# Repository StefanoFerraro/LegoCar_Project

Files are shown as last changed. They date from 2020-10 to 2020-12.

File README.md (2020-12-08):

# **LegoCar Project**

Lego Car Demo (https://www.youtube.com/watch?v=NI2pKg-ZRkI)

**^^^ Click for opening the video**

Inspired by the Donkey Car project, I introduce the Lego Car project. The goal of the project is to design and develop an autonomous car build with elementary pieces of Lego and keeping everything else on a budget.

From the hardware side, the system is based on: **Raspberry Pi4b** for controlling the motors (steering / throttling) and running the perception algorithms  + **L298n** as motor driver + **Picamera** for perception + **Xbox360 Controller** used for manual control/autopilot enable. 

The software development is based on the **ROS** framework, code has been written both in **C++** and **Python**. Driver/Controller libraries has been written for this specific hardware/configuration (feel free to ask if you need help with your specific configuration).

## **1 - Software Overview**

### **1.1 - Structure**

* [**l298n_drive**](l298n_drive): ROS package (C++) for interpreting /cmd_vel messages and converting it into actual motion.
* [**xb360_teleop_interface**](xb360_teleop_interface): ROS package (C++) for interpreting /joy messages and converting it into a /cmd_vel message.
* [**lane_detection**](lane_detection): ROS package (Python) running the perception algorithm. 

### **1.2 - Packages Dependencies**

The following project require the integration of existing ROS packages/libraries:
* [**WiringPi**](http://wiringpi.com/): ROS library (C) for RPi GPIO access
* [**raspicam_node**](https://github.com/UbiquityRobotics/raspicam_node): ROS package for image acquisition from Picamera, the image stream is published as a message of type Sensor_msgs/CompressedImage. 

## **2- Hardware Overview**

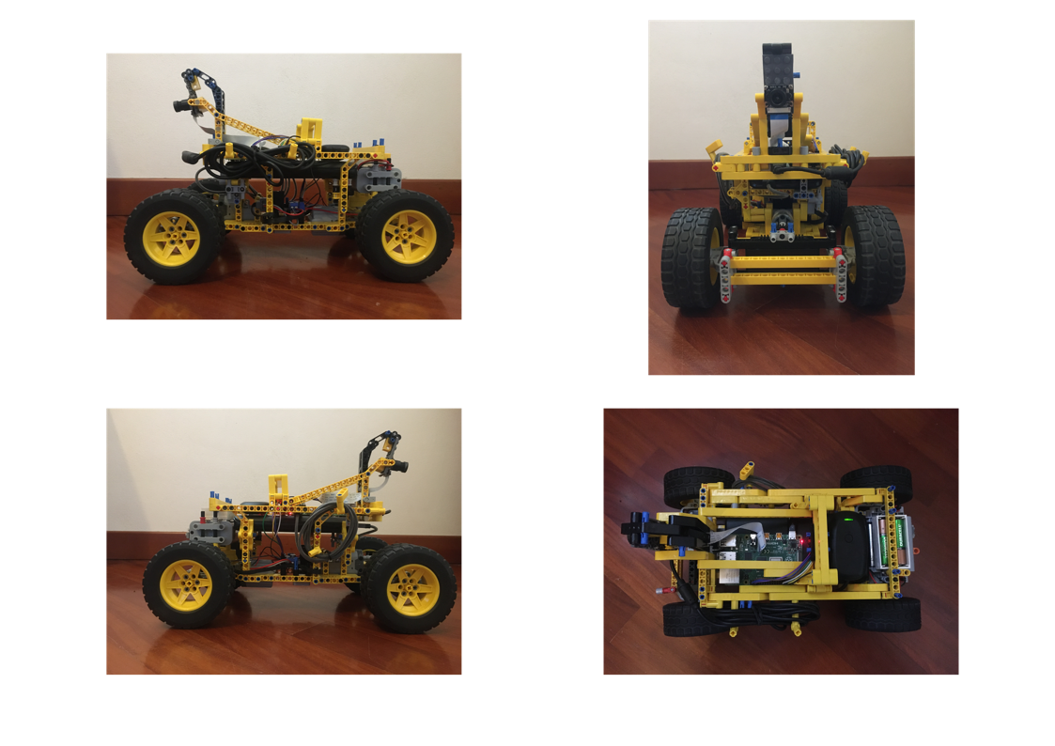
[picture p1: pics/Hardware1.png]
Hardw1


The Lego car model has been custom build for this specific project, it consist of a rear traction system (with differential steering), and a simple steering system in the front. A good starting point for a similar design is proposed here: [Fast and Compact LEGO PF RC car](https://www.youtube.com/watch?v=oS-6K2MqfjM). All the Lego pieces used in the construction were already available to me, almost all the parts comes from the 42030 Lego kit. The overall design of the car presented in this project is the result of multiple iterations. 

### **2.1 - Motors and Battery Pack**
A [Lego Power Function XL Motor](https://www.lego.com/it-it/product/lego-power-functions-xl-motor-8882) has been used for the traction system. For the steering system, a servo motor was needed in order to have precise control over the steering angle, I opted for a [Lego Power Function Servo Motor](https://www.lego.com/it-it/product/power-functions-servo-motor-88004), this specific motor has 15 fixed positions from +90° to -90°. 

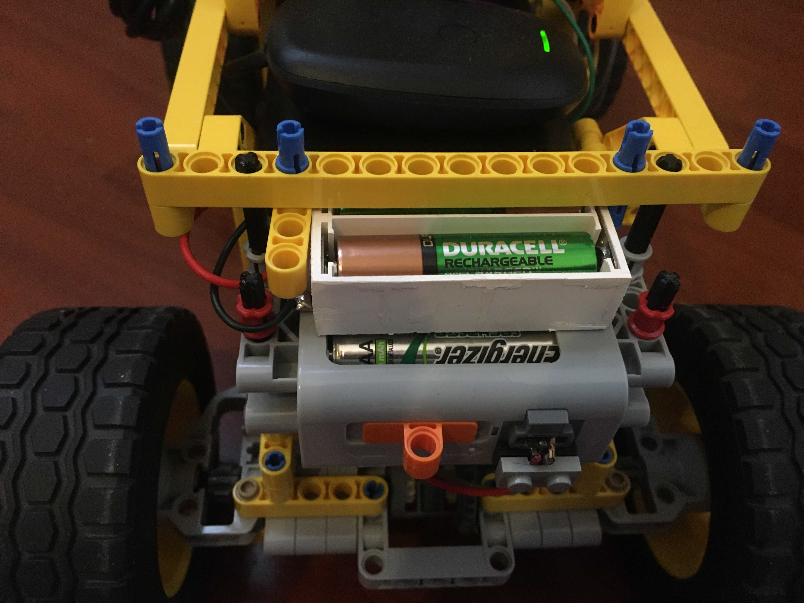
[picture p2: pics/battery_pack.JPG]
battery


Both motors are powered via the [Lego Battery Box](https://www.lego.com/it-it/product/lego-power-functions-battery-box-8881), that has been extended with two batteries in series for a total of 8, this in order to output the required voltage of 9V (Lego recommend 9V for this motors), also with rechargeable Ni-MH batteries (1.2V): 



This mod is not needed in case of non-rechargeable Ni-MH batteries (1.5V): 



In the long run the rechargeable solution is preferable due to the high demand of power (with the rechargeable solution I run the system for approx. 30 minutes before having a consistent decrease in maximum speed).

In order to connect all the components without rewiring all the cables, and therefore limiting the future use of the motor, I come up with a clamping system that consist of forcing the reinforced cable end into the desired pin and taking everything in place thanks to a modifies Lego flat 2x1.  

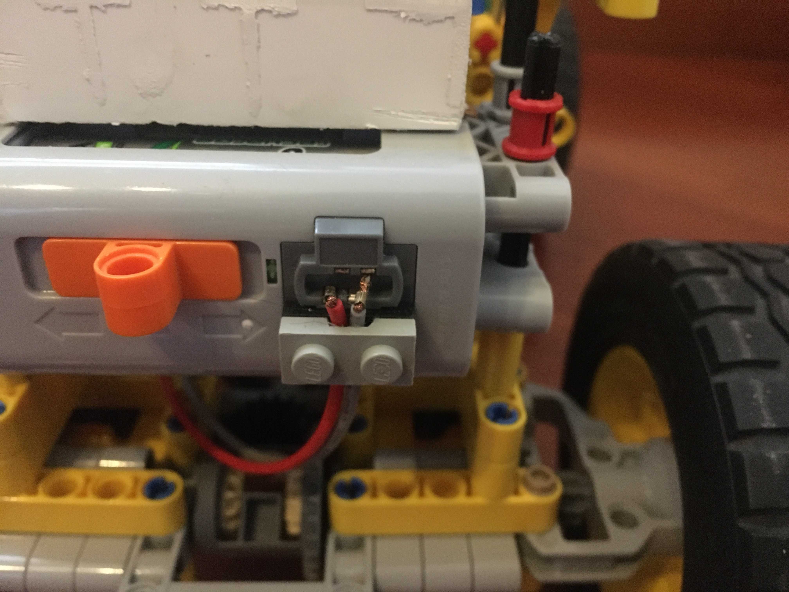
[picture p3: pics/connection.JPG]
connect


### **2.2 - Motors Driver**

A **L298n** module is used in order to control the XL function motor and the Servo one. The later has a control electronics slightly different from the classic 3 wires servo, it consist of 4 wires, one wire controls the servo in the clockwise direction (0..+90°) and the other along the anti-clockwise (0..-90°).

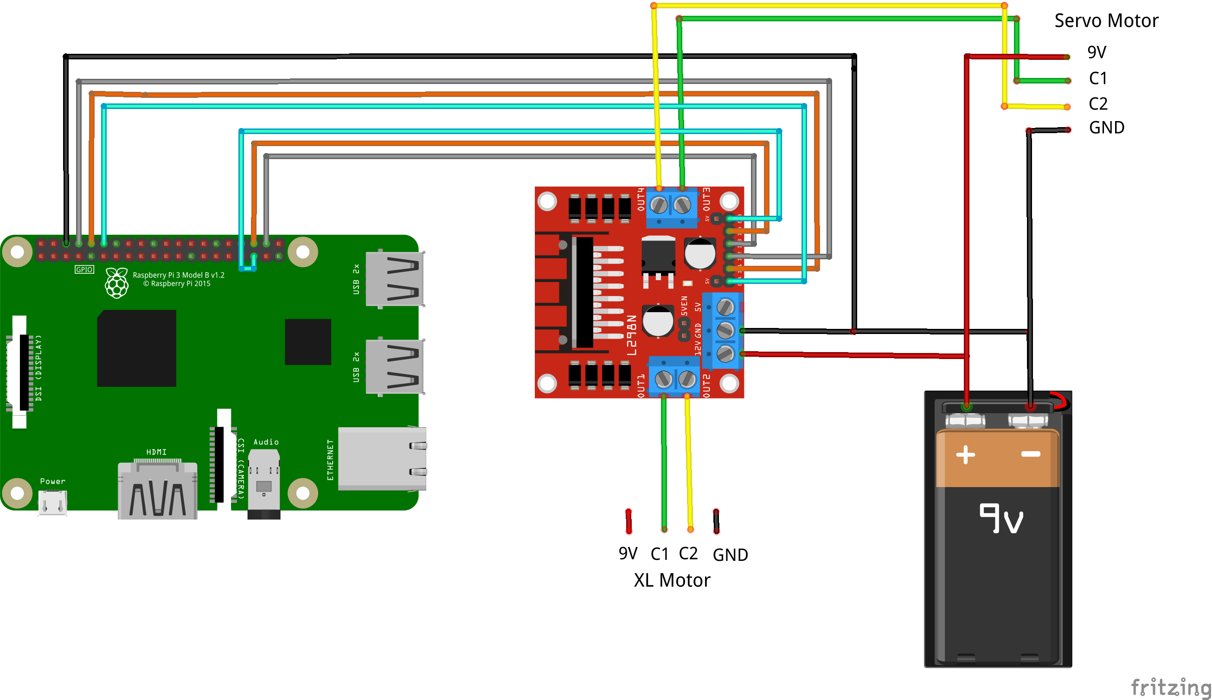
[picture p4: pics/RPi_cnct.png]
wiring


motor_detail

As a reference for the wiring and further technical information about Lego motors/servo: [Lego Technical Information](https://www.philohome.com/tech.htm). Below, the Lego connector scheme is shown:  

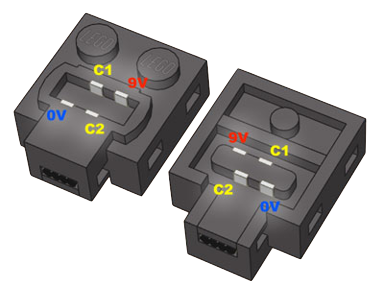
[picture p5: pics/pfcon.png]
lego_wires


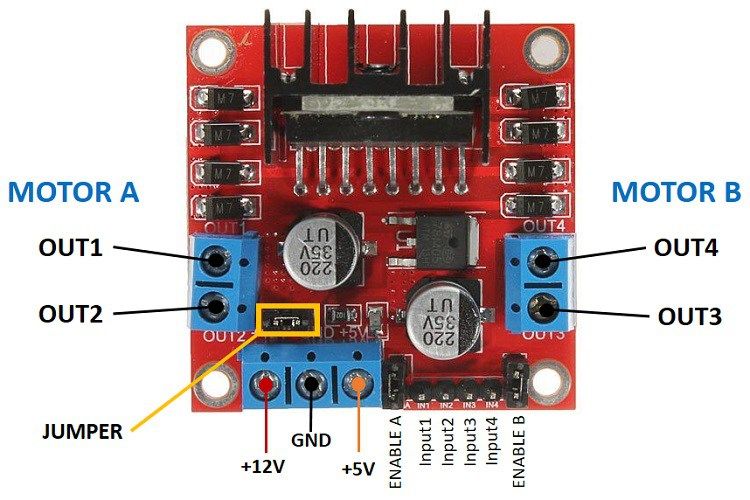
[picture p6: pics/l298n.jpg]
l298n


`OUT3` and `OUT4` of the l298n are wired respectively to `C1` and `C2` of the servo. The same applies to `OUT1` and `OUT2` for control ports of the XL motor. 

In a **DC motor (XL motor)** RPM (Revolutions-Per-Minute) can be module controlling the voltage. PWM (Pulse-Width-Modulation) signal can be used to control the voltage that goes through the motor. Varying the duty cycle of the PWM signal varies also the average voltage outputed (i.e. RPM of motor). 

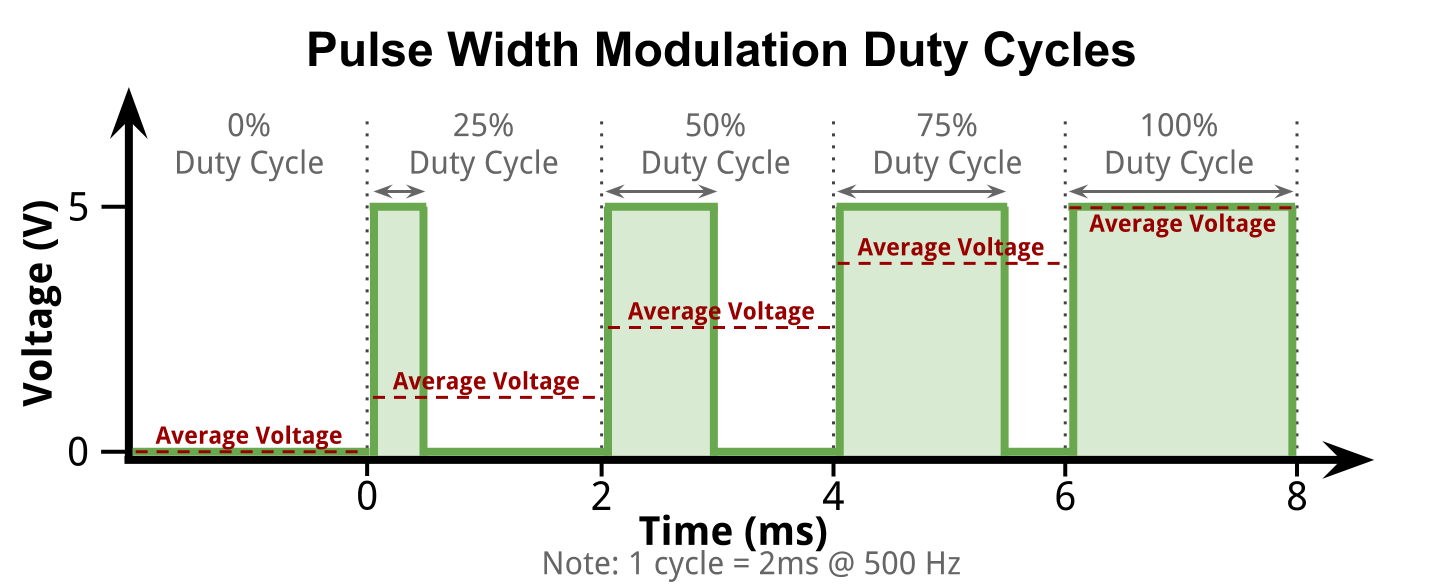
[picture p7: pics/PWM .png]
PWM


With respect of the l298n functional scheme, `Input1` and `Input2` are used for controlling forward/backward direction instead the PWM signal is sent through the `EnableA` pin for the RPM control. Here is a summary table for the control of the XL motor:

| Motion | Input1 | Input2 | EnableA (PWM duty cycle %) |
|---|---|---|---|
| Forward  | 1 | 0 | 0..100 |
| Backward | 0 | 1 | 0..100 |
| Brake | 1 | 1 | 100 |
| Float | 0 | 0 | 0 |

**Servo modules** exploits PWM signals for controlling the position of the axis. In a servo each fixed position of the axis correspond to a specific duty cycle, usually in a common servo system the control goes from -90° to +90° using just one wire. As previously said, in the Lego Servo motor we have 2 control wires, one for clockwise positions and the other for anti-clockwise, here the principle is well presented: [Controlling LEGO Power Functions Servo Motor](https://www.youtube.com/watch?v=XQskgJjk5S4).  

With respect of the l298n functional scheme, `Input3` and `Input4` are used for controlling clockwise/anticlockwise direction instead the PWM signal is sent through the `EnableB` pin for the position control. Here is a summary table for the control of the Servo motor:

| Position | Input3 | Input4 | EnableB (PWM duty cycle %) |
|---|---|---|---|
| 7 (90°) | 0 | 1 | 100 |
| 6 | 0 | 1 | 88.2 |
| 5 | 0 | 1 | 76.0 |
| 4 | 0 | 1 | 63.5 |
| 3 | 0 | 1 | 50.1 |
| 2 | 0 | 1 | 38.0 |
| 1 | 0 | 1 | 25.8 |
| 0 (0°) | 0 | 0 | 0 |
| -1 | 1 | 0 | 25.8 |
| -2 | 1 | 0 | 38.0 |
| -3 | 1 | 0 | 50.1 |
| -4 | 1 | 0 | 63.5 |
| -5 | 1 | 0 | 76.0 |
| -6 | 1 | 0 | 88.2 |
| -7 (-90°)  | 1 | 0 | 100 |

**Raspberry Pi4** has 4 IO that can output hardware PWM signals (as reference see: [Raspberry Pi GPIO](https://www.raspberrypi.org/documentation/usage/gpio/)). In this project I have used (in BCM notation) GPIO19 and GPIO18 as output PWM channels, GPIO14, GPIO15, GPIO16, GPIO20 as standard output channels.  

### **2.3 - PiCamera**

The camera used was already available to me (reused from another project), it has a 75° vision angle, with IR features ([Camera Link](https://it.banggood.com/Camera-Module-For-Raspberry-Pi-4-Model-B-or-3-Model-B-or-2B-or-B+-or-A+-p-1051437.html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)). In the donkey car project they are using a wide angle lens (120/150° angle) in order to get a better vision around the car, this can be useful in order to have more information about the environment in one pic, but also can 'distract' the perception algorithm with useless informations. We will discuss further this aspect in the perception algorithm repo.

The camera, has been fixed using little screws onto a planar lego piece, that is part of a adjustable inclination mount.

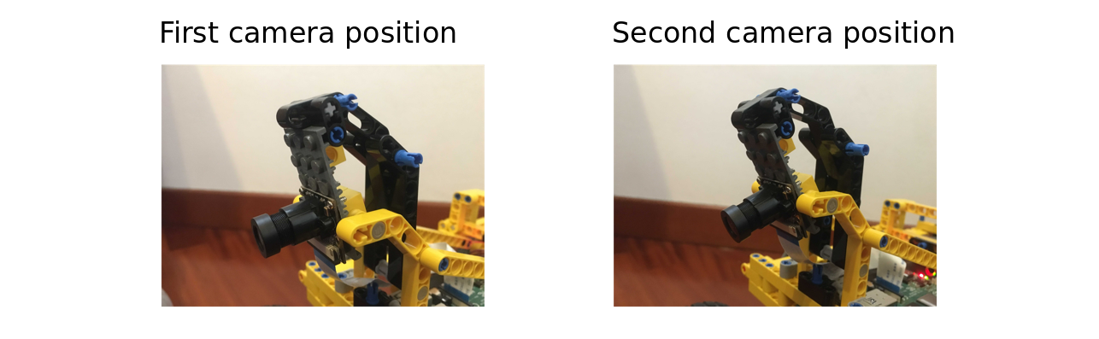
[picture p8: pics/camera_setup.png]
camera_setup


### **2.4 - RPi and Xbox Controller**

The Raspberry Pi is powered by a second battery that outputs 5V/3A as requested by the RPi. The battery serves also as mounting support for the RPi and the controller receiver.

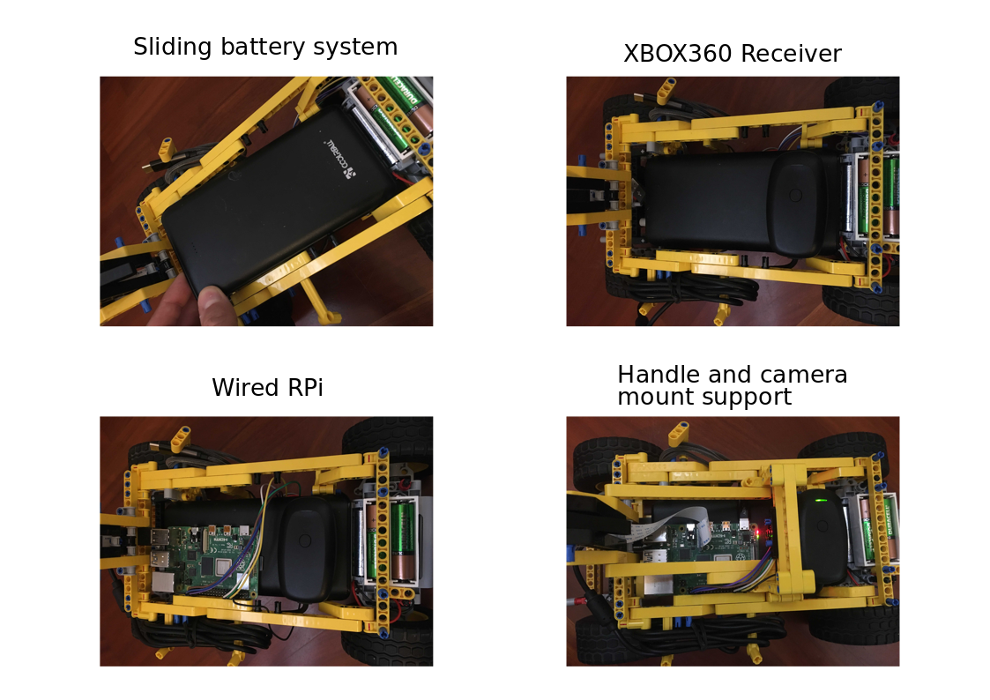
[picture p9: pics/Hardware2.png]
hardware2


In the images above the is shown the sliding system of the battery, this guarantee an easy access to the electronics below when needed. The Xbox360 receiver is fixed in place using patafix. An handle has been designed in order easily transport the car manually.

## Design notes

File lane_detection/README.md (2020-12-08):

# **Lane Detection**

Lego Car Demo (https://www.youtube.com/watch?v=NI2pKg-ZRkI)

**^^^ Click for opening the video**
 
The package provide lane detection functionalities for the compressed image coming from the `raspicam_node`. A direction angle is computed and outputted with the topic `/steering_angle`. A processed image is published to the `/lane_detection/image/compressed` topic.
The Implementation presented is based on several filters applied to the image, and the subsequent application of Canny algorithm + Hought transform. 

## **1 - Main dependencies**
 
* sensor_msgs/CameraInfo
* sensor_msgs/CompressedImage
* rospy
* numpy
* opencv (cv2)
* line_detect/steering_angle

## **2 - Functionalities**

The package subscribe to the topic `/raspicam_node/image/compressed` (type sensor_msgs/CompressedImage), published by the raspicam_node package. Messages are published on topic `/steering_angle`, a custom message designed for passing direction information to the PD controller.

The acquired image go through a specific pipeline in order to extract the the lane/s from the scene. Lanes are then implied in the computation of a direction vector for the LegoCar. The output of the pipeline process is then published to the `/lane_detection/image/compressed` topic.

The pipeline of the image analysis process is:

 1. **Image acquisition and undistortion process**
 2. **Filtering image (blacks)**
 3. **Edge detection wt Canny algorithm**
 4. **ROI + Lines detection wt Hough transform**
 5. **Computation of middle line**
 
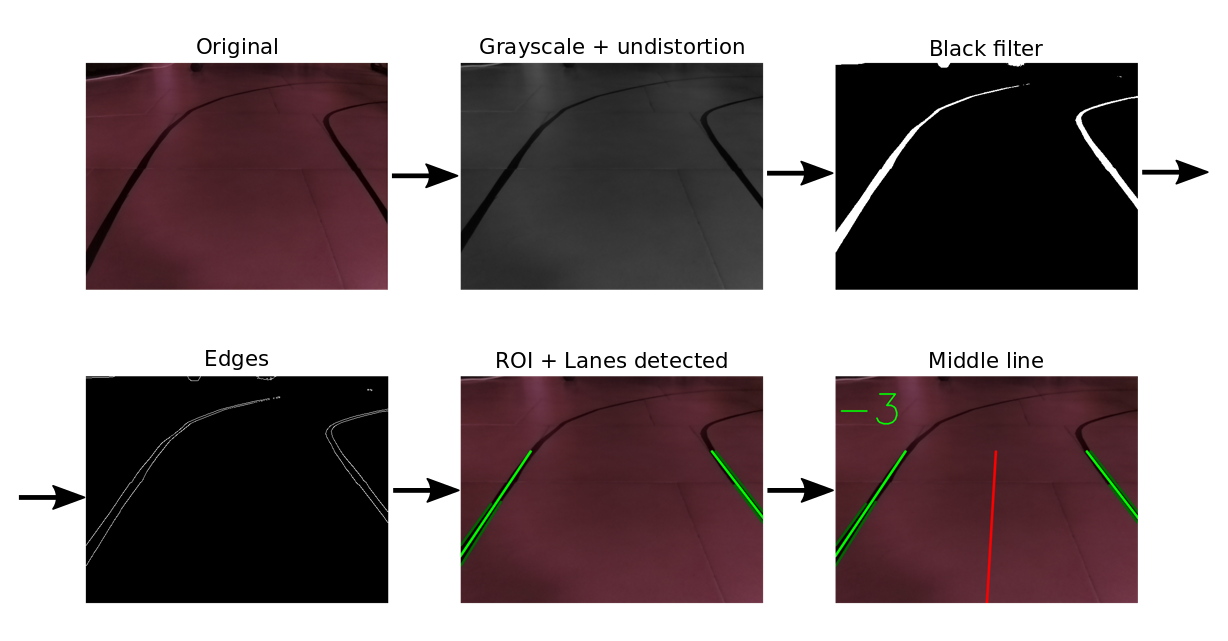
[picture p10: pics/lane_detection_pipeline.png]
 

### **2.1 - Image acquisition and undistortion process** 

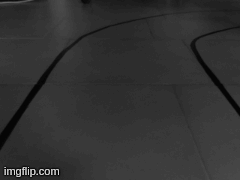
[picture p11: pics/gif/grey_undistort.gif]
greygif
 
 
Cameras transform 3D space information into a 2D form. Since this process is not perfect (due to the imperfect production process of the lenses), we cannot trust the information coming straight from the camera as it is. Our goal is to position the car in space, in order to do it properly the camera matrix and the distortion coefficient needs to be computed and both compensated.
 
The `raspicam_node` package contains a calibration tool, called [`camera_calibration`](https://github.com/UbiquityRobotics/raspicam_node), a calibration maze is needed for this process. Once the process is completed a `.yaml` file is generated. Follows an example:

````
image_width: 640
image_height: 480
camera_name: camerav2_640x480
camera_matrix:
  rows: 3
  cols: 3
  data: [724.7065317897147, 0, 329.1544084760975, 0, 723.9111589306867, 222.2659871640654, 0, 0, 1]
distortion_model: plumb_bob
distortion_coefficients:
  rows: 1
  cols: 5
  data: [-0.425024653765871, 0.2275022820178016, -0.0009324566898835676, 0.002125165132523941, 0]
rectification_matrix:
  rows: 3
  cols: 3
  data: [1, 0, 0, 0, 1, 0, 0, 0, 1]
projection_matrix:
  rows: 3
  cols: 4
  data: [661.0226440429688, 0, 332.2321572900546, 0, 0, 688.1121215820312, 220.1584891049697, 0, 0, 0, 1, 0]
````

From this file we are going to extract `camera_matrix` and `distortion_coefficient`. Th function `undistort` (in the `callback` function) from the `OpenCV` library, will then rectify the original image. Below an example of the process where an horizontal line has been added as a reference, looking closely we can notice how the floor joints in the original image has a parabolic trend, instead in the rectified one they are perfectly straight.  

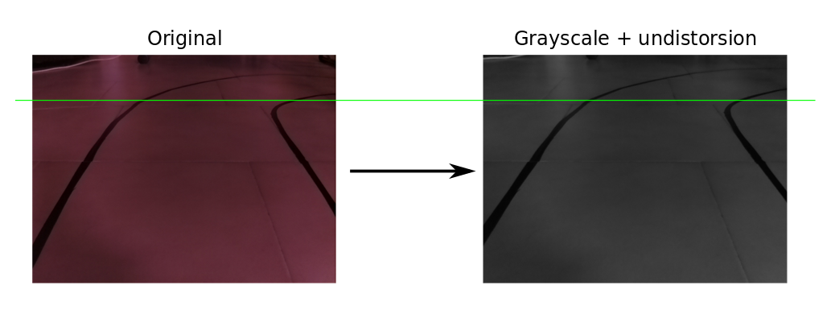
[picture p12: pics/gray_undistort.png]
 
 
Before proceeding a `COLOR_BGR2GRAY` color conversion has been applied in order to decrease the number of color channels and concurrently the computational weight for each image. 

### **2.2 - Filtering image (blacks)**

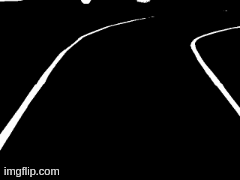
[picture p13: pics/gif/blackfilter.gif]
blackgif


In order to increase the precision of the perception algorithm a further filtering of the image is required. This has been accessed after the first tests of the algorithm where the floor joints where detected as reference lanes, compromising the result. The solution was to filter out every pixel above a certain range of the gray scale.

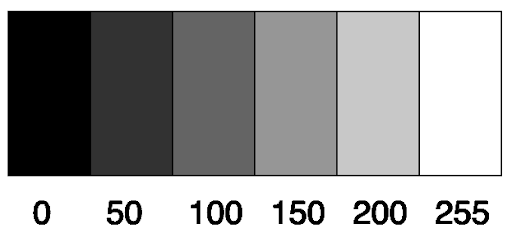
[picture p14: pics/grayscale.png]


We are going to create a mask with all the pixels below `50` in the grayscale, an optimal value for filtering out just the floor joints. This filter method has some dependents on the light conditions. In order to have consistent light conditions, all the tests has been carried in-house, with no interference from the sun light (artificial light constant). The output mask represent in white the black pixels of the source image. 

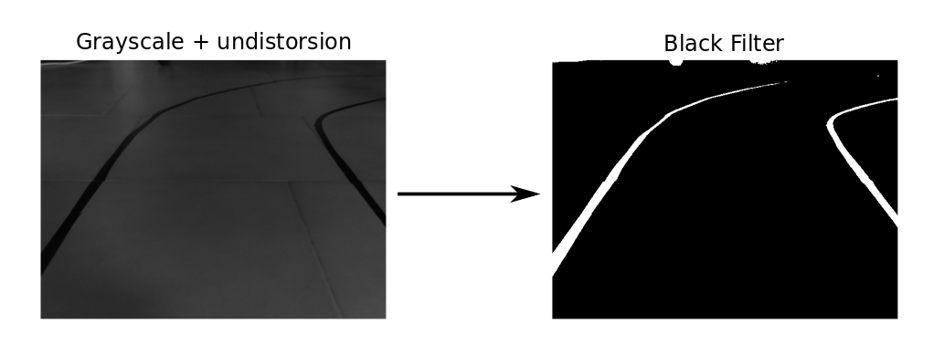
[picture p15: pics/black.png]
black

 
### **2.3 - Edge detection wt Canny algorithm**

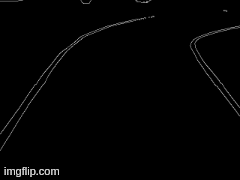
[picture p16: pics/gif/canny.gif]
 

The next step consist in applying the Canny algorithm for performing edge detection. The Canny algorithm consist of different steps, processed internally from the function `Canny`:

 1. **Noise Reduction**: The image is blurred thanks to a Gaussian filter (5x5), this aims to reduce pixel level noise.
 2. **Intensity Gradient**: A Sobel kernel is applied to the entire image both vertically and secondly horizontally resulting in two gradients matrix <em>Gx</em> and <em>Gy</em>. 
 
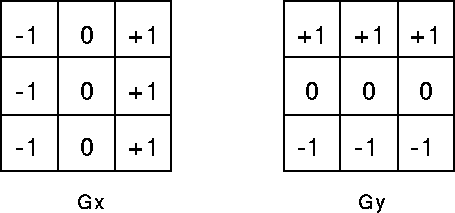
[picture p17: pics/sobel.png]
sobel
      
 
    The Sobel kernel extract any vertical or horizontal edge depending on the kernel adopted.
 
     Both gradients are then combined to obtain the <em>Edge Gradient = </em>
 
     .
 
     The direction of the gradient is given by <em>Angle = </em> 

     

3. **Non-Maximum Suppression**: This step is required in order to have a one pixel edge instead of considering redundant pixels signaling the same edge.

4. **Hysteresis Thresholding**: Last step of the algorithm consist in selecting which edge we want to take and which discard. The threshold value consist of the gradient intensity, any edge below a certain minimum value is discarded instead any edge above a maximum value is taken. Anything in between this two limits are kept if they are connected to a over-max edge.

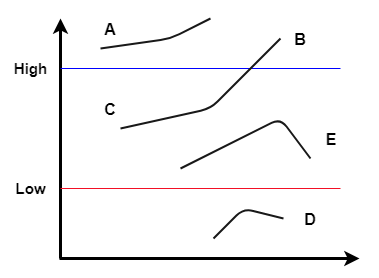
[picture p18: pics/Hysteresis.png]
hyst
      
 
     Considering the picture above, **A**, **B/C** are going to be taken as edges, instead E and D discarded.
 
The `Canny` function implemented in OpenCV requires only (in addition to the image to process) the Max and Min threshold. The ones used in the project derive form a initial tests where the car has been placed in ideal conditions.

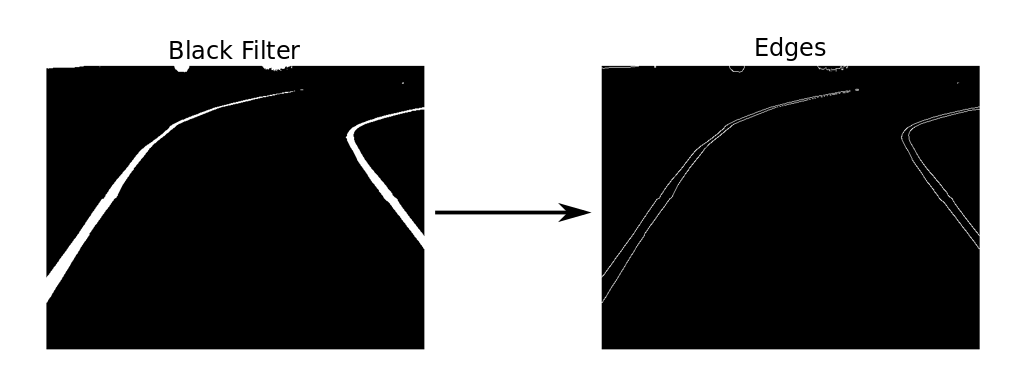
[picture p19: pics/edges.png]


###  **2.4 - ROI + Lines detection wt Hough transform**

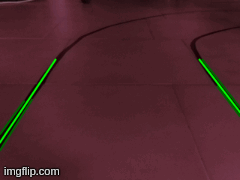
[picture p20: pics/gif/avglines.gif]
 

Next step in the pipeline consist in selecting a ROI (Region Of Interest), this helps the system eliminate noise information from the image (surroundings and long distance lanes), keeping only the relevant part. The shape of the ROI is shown in the image below (blue rectangle), the height of the rectangle is the 66% of the total height of the image.

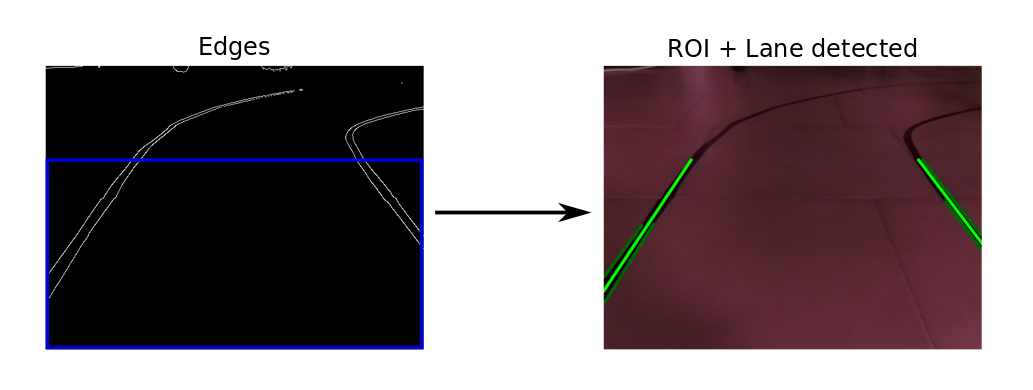
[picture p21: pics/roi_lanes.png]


The image is now in the ideal situation to perform the actual lane detection. In order to do that we are going to use the Hough transform, an algorithm specifically developed for identifying straight lines. 

The algorithm consist in analyzing each pixel of the image and identifying if the specific pixel is part of a straight line. In order to do that, all the lines that goes through a specific pixel are considered, confronting all the lines from all the points, the algorithm extrapolate the lines that are in common between all the point (i.e. the points are part of the same line). In this process the user has to specify the minimum number of pixel to share the same line, this is required in order to eliminate noise.

In order to have an efficient lane detection we need to perform an edge detection previously. In this way the hough transform is going to consider only the edges detected and not all the pixel of the image.

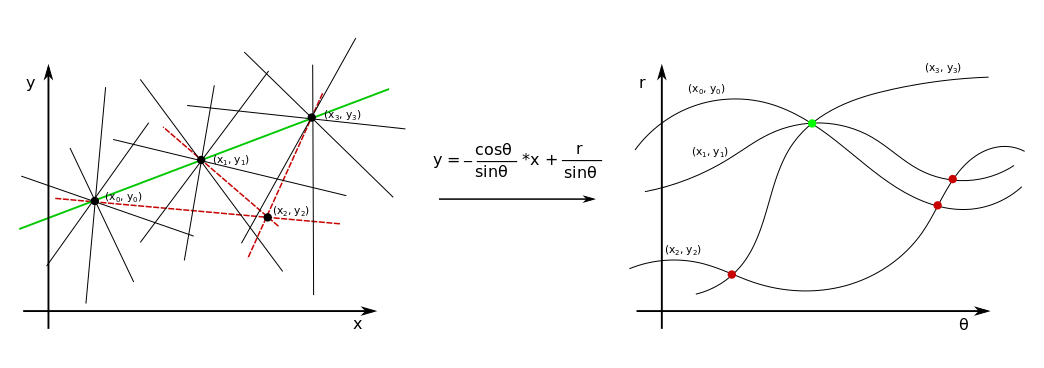
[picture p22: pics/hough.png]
hough
 
 
 In the image above we have four pixel considered, the algorithm, as said, consider all the lines passing through each specific pixel and picks the one that is in common. Here the minimum threshold in order to output a line is that it has to be shared among at least 3 pixels. The green line is output the final output, instead the dashed red lines are considered but discarded by the algorithm, because they do not reach the minimum threshold.
 
In order to visualize this phenomena more easily we can refer to the **Polar coordinate system**, where each curve represent all the combinations of lines through a specific point. In this space an intersection between two curves, identify a shared line between pixels. The more intersections in the same region stands for more pixels sharing the same line i.e. the longer the identified line. 

OpenCV provide two main implementations of this algorithm the first `HoughLines()` is the standard implementation and output, in polar coordinate the coefficients for the identified lines. The second, a more efficient implementation, is the **Probabilistic Hough Transform** `HoughLinesP()` that output start and end point of the detected line.

The parameters to input are:
`HoughLinesP(image, rho, theta, threshold, MinLinLength, MaxLineGap)`

 - **image**: output of the edge detector process
 - **rho**: the resolution for the parameter `r` (Polar coordinate) (usually 1, if incremented adjacent lines, along the r axis, are grouped together)
 - **theta**: the resolution for the parameter `theta` (Polar coordinate) (usually PI/180, if incremented adjacent lines, along the theta axis, are grouped together)
 - **threshold**: the minimum number of intersection (in polar coordinate) to "detect" a line
 - **MinLinLength**: The minimum number of points that can form a line. Lines with less than this number of points are disregarded. Usually if the r and theta resolution is the minimum, this parameter should coincide with the threshold.
 - **MaxLineGap**: Maximum gap between two pixels to be considered part of the same line.
 
Again as for the Canny edge detector the best way to pick these parameters is by experience, setting a fixed test environment and tunning them.

Applying these algorithm is going to output a series of segments of lines. The bare output of this function is shown below, printed in the original image. A function have been designed in order to merge lines together in order to obtain maximum 2 main lines. The discriminant for the grouping is the slope of the single segments. From the code the function `Average_lines` takes in all the lines segments, compute the slope and coefficient of them, group them based on the slope sign and compute an average slope. Based on the segments detected we can have 2 average lines output, 1 average line output or 0. Finally the function `Points_of_lines` takes case of computing two points (bottom and top edge of the ROI) of the average line for plotting purposes.

Below are shown two example of how the implementation handles different scenarios.

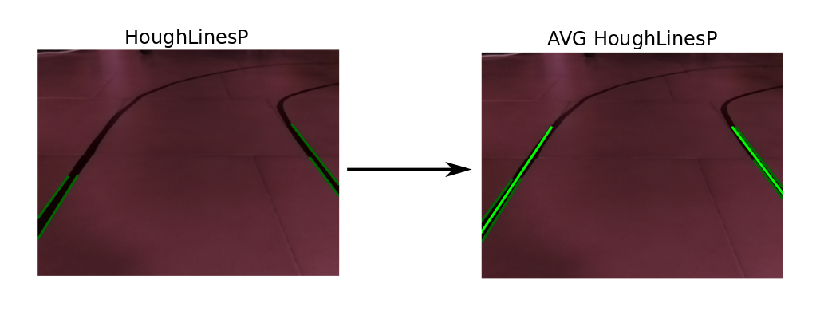
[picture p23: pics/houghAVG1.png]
houghAVG1

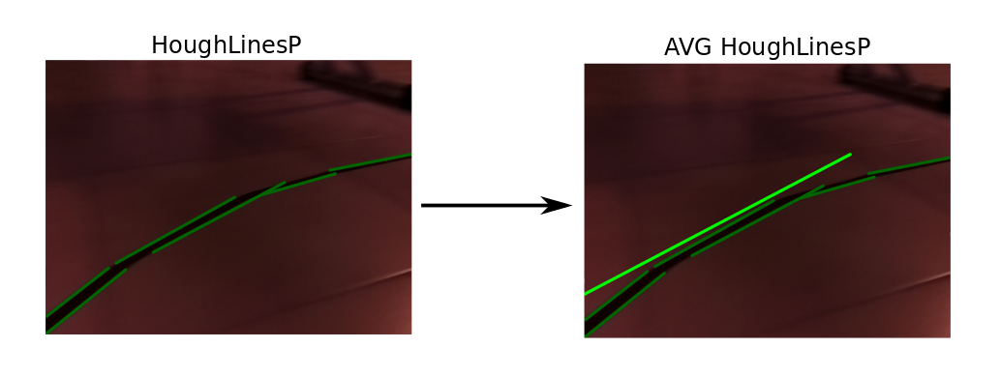
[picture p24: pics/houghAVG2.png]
houghAVG2


### **2.5 - Computation of middle line**

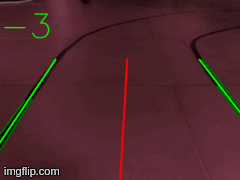
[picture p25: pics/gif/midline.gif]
midgif


The final step consist in computing the middle line useful for directing the car. The middle line angle with respect to the vertical axis is directly related to the steering that needs to be applied in order to have the car at the center of the both lanes. In order to analyze this last part of the pipeline, let's split the analysis in 2 main scenarios: two average Hough lines are identified, one average Hough line is identified.

#### **Two average Hough lines**
In this case the computation of the middle line is trivial. Indeed, it consist in averaging the top points of both lines and keeping fixed the bottom one exactly to the middle of the image, this because the camera origin is placed exactly in the center of the car, so when the car is placed in the middle of the lanes we want to have e middle line to be perfectly vertical. When the car is not at the center of the track, we would have a line that directs the car to the center. By averaging the top points of the ROI 

#### **One average Hough line**
In this scenario we have relative position just from one of the lanes, so it is impossible to position the car in space without further informations. Since the track has a constant width we can assume that the width as a complementary information for positioning the car. Indeed, the upper point of the line is given by considering the Hough line upper point and then adding the half of the constant width of the track projected in the 2D space of the image.
For the bottom point, as for the previous scenario, it is fixed to the middle of the image frame.

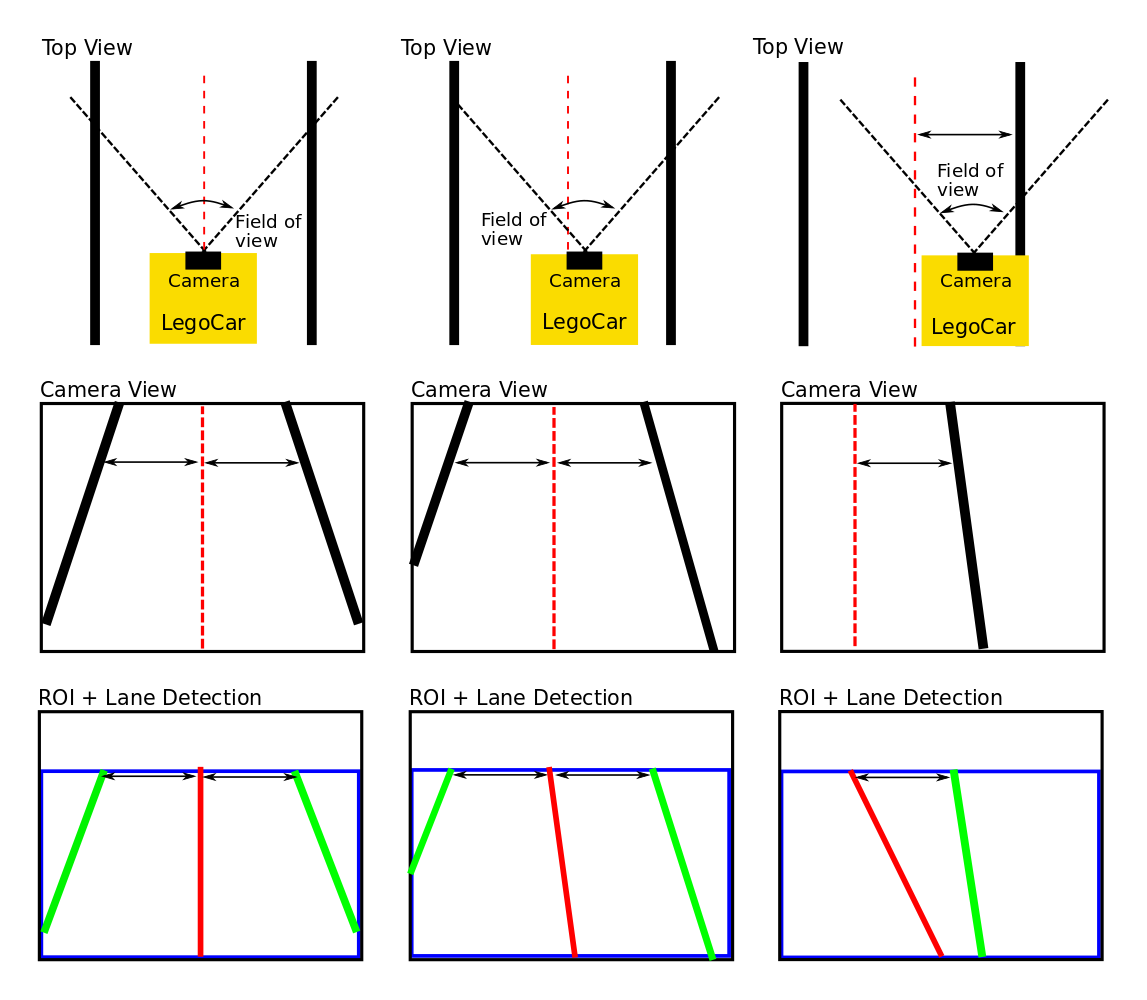
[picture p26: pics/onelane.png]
onelane


We need to extract the constant width of the track projected in the 2D at a specific image frame height (top of ROI), in order to do that a ROS video bag, of a manual ride, has been analyzed and data point where both hough lines where present are considered. The distances are here presented:

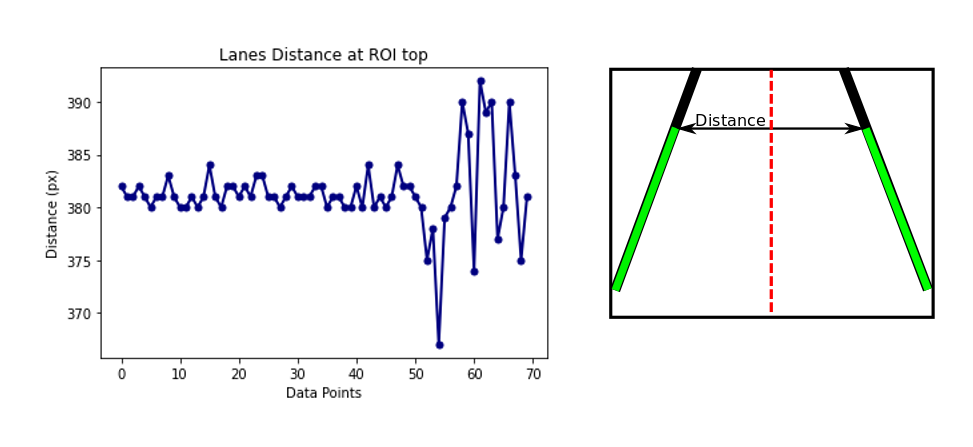
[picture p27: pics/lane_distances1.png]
lanedistances


We have a mean distance of around 380px between, the lines.

Last thing to do is extract the angle between the middle line with respect to the vertical direction. This is then published to the `/steering_angle` topic, and plotted to the published processed image send to `/lane_detection/image/compressed`.

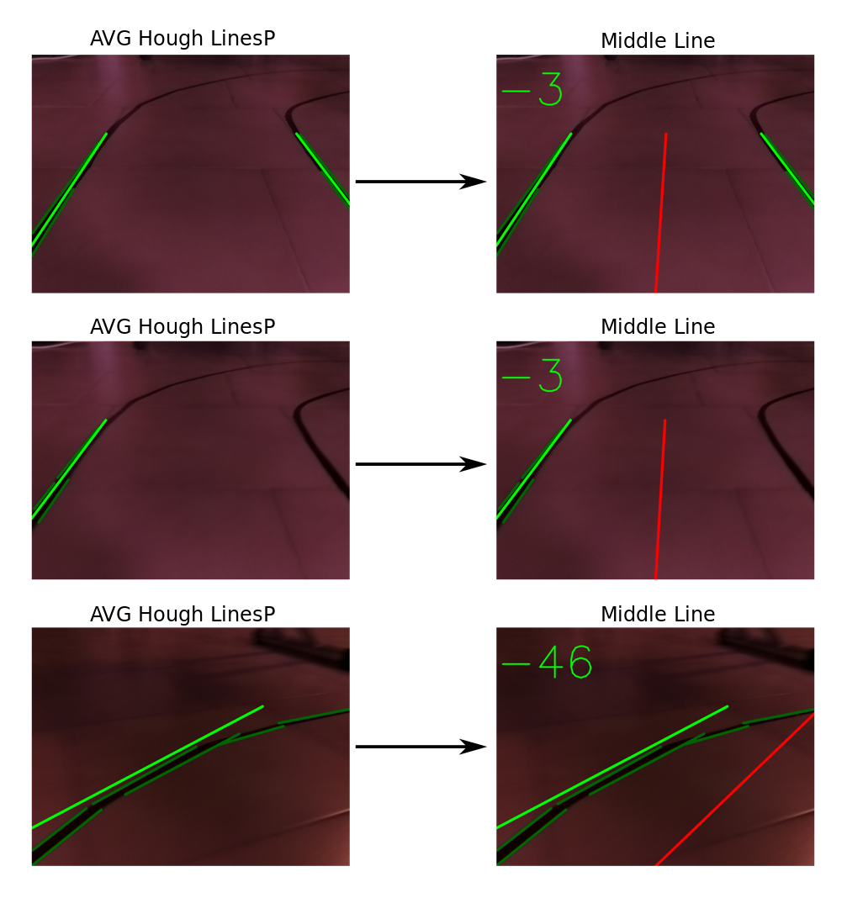
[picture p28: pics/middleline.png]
middleline


From the image above notice how the system behave similarly when dealing with one or two lines detected.

## **3 - Conclusion and final thoughts**

This part was the hardest part of the project, which involved the tuning of several parameters by hand. With the traditional Computer Vision approach I was able to develop a strong intuition for what worked and why. I also learnt that the solutions developed through such approaches aren't very optimised and can be sensistive to the chosen parameters. As a result, I developed a strong appreciation for Deep Learning based approaches to Computer Vision. Although, they can appear as a black box at times Deep learning approaches avoid the need for fine-tuning these parameters, and are inherently more robust.

The challenges I encountered were almost exclusively due to non-uniform lighting conditions, shadows, discoloration and presence of floor joints. I had to constrain the test environment isolating any source of external light, and applying a uniform source of artificial light. Testing the functionality of the car in this control environment proved the good implementation of the pipeline.

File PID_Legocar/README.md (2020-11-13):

# **PID Controller Lego Car**

The package provide a functional interface between the line detection package and the l298n driver. The `/steering_angle` message coming from the line detect model is used for direct control of the steering of the LegoCar, a PD controller ('I' contribution present but not used) has been used in order to adjust throttling while steering.

## **1 - Main dependencies**

* geometry_msgs/Twist
* sensor_msgs/Joy
* ros/ros
* line_detect/steering_angle

## **2 - Functionalities**

The package subscribe to the topic `/steering_angle` (type line_detect/steering_angle), published by the [line detect](../line_detect) package. Messages are published on topic `/cmd_vel` (type geometry_msgs/Twist).

Subscription to the `/joy` topic is required for having a enable button (in this case the **B** button of the xbox360 joystick) in order to switch on/off the following controller.

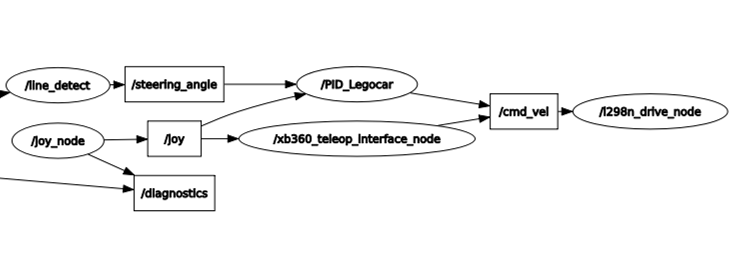
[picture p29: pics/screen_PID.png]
screen


Key parameters are loaded from the configuration file [config.yaml](../config/config.yaml).

A message of type of type geometry_msgs/Twist is composed of the following parts:

#### **Steering**

`cmd_vel_msg.angular.z = -Ca*steering_angle.ang`

`steering_angle` come from the line_detect package. The steering command given is just a linear derivation of the msg steering_angle (Ca is a coefficient). 

#### **Throttling**

`cmd_vel_msg.linear.x = -def_vel - PID_module(steering_angle.ang)`

At a fixed speed, when the car steers the speed is reduced. For this reason throttling consists of two contributions: a fixed part (`def_vel`) + a variable part controlled by a PID controller and dependent on the steering_angle msg.

In this specific case a PD controller has been used since the 'I' contribution is not needed for a correct functionality of the car.

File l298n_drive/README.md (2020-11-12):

# **L298n Driver Library**

The package provide a basic l298n driver library for converting geometry_msgs/Twist messages into Legocar movements.

## **1 - Main dependencies**

* geometry_msgs/Twist
* wiringPi
* ros/ros

## **2 - Functionalities**

The package subscribe to the topic `/cmd_vel` (type geometry_msgs/Twist), published by [xb360_teleop_interface](../xb360_teleop_interface). It gives direct access to the GPIO of the RPi and controls the output ports, wired to the l298n module.

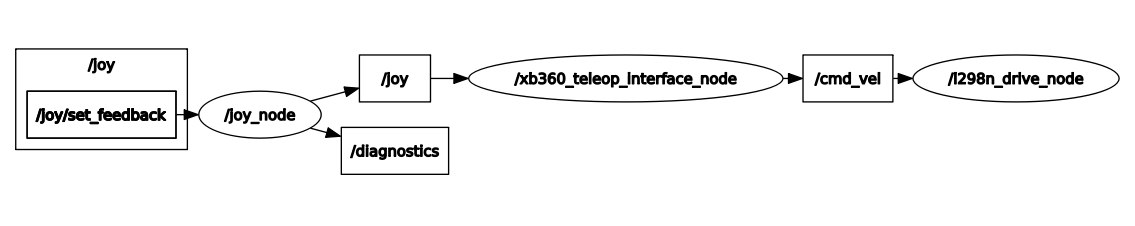
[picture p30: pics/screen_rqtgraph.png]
screen


This library exploit [WiringPi](http://wiringpi.com/) to get access to the GPIO ports, in particular for the ports that require a PWM, administrator permission is required, for this reason in the launch file of the Legocar we have:

````xml 
<node pkg="l298n_drive" name="l298n_drive_node" type="l298n_drive" output="screen" launch-prefix="sudo -E LD_LIBRARY_PATH=$(optenv LD_LIBRARY_PATH)"> </node>

````

Prefix consist of `sudo -E` for running the node with administrator privileges, preserving the environment when running the command (WITH some exception, variables like PATH, LD_LIBRARY_PATH, ecc. are not preserved).  Moreover we need to specify the library path `LD_LIBRARY_PATH`, that is not preserved in as environment variable. 

Refer to the following table for the linear motor control:

| Motion | In1 | In2 | EnA (PWM duty cycle %) |
|---|---|---|---|
| Forward  | 1 | 0 | 0..100 |
| Backward | 0 | 1 | 0..100 |
| Brake | 1 | 1 | 100 |
| Float | 0 | 0 | 0 |

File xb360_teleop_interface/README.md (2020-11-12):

# **Xbox360 Controller Interface**

The package provide a functional interface for the control of the Legocar. Standard interfaces are also available for the xbox360 controller ([teleop twist joy](http://wiki.ros.org/teleop_twist_joy)), unfortunately I found them overcomplicated for the control of the car.

## **1 - Main dependencies**

* geometry_msgs/Twist
* sensor_msgs/Joy
* ros/ros

## **2 - Functionalities**

The package subscribe to the topic `/joy` (type sensor_msgs/Joy), published by the [joy node](http://wiki.ros.org/joy). Messages are published on topic `/cmd_vel` (type geometry_msgs/Twist).

screen

The published message contains two main coordinates `cmd_vel.linear.x` that is going to be used for the throttling of the car and `cmd_vel.angular.z` for the steering.

The mapping of the bottons/axis can be modified in the header file [include/xb360_teleop_interface.h](include/xb360_teleop_interface.h): 

```` C++
int enable_button = 0;
int forward_axis = 5;
int backward_axis = 2;
int angular_axis = 0;
````

following the table below: 

| Button Index | Button name | Axis Index | Axis name |
|---|---|---|---|
|  0 | A |  0 | Left/Right Axis stick left  |
|  1 | B |  1 | Up/Down Axis stick left |
|  2 | X |  2 | LT |
|  3 | Y |  3 | Left/Right Axis stick right |
|  4 | LB |  4 | Up/Down Axis stick right |
|  5 | RB |  5 | RT |
|  6 | back |  6 | cross key left/right |
|  7 | start |  7 | cross key up/down |
|  8 | power | | |
|  9 | Button stick left | | |
|  10 | Button stick right | | |

When the node is run information about the controller buttons/axes are printed:

screen

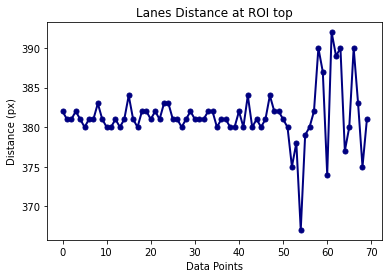
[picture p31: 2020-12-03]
pics/lane_distances.png

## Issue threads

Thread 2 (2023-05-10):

Is this compatible with other camera ?

hanselhermawan, 2023-05-10:
Hey, I have tested the code and it runs well. But it didn't open the camera visual on the screen as I already run the code. I'm wondering if this was about the camera that I used (I using a PS3 eye camera).

Thanks

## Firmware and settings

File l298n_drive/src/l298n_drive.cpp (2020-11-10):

/**

\authors   		Ferraro Stefano <ferrarostefano@rocketmail.com>

\date			10/10/2020

\description	The package provide a basic l298n driver library for converting geometry_msgs/Twist messages into Legocar movements.

*/

#include <wiringPi.h>
#include <geometry_msgs/Twist.h>
#include <ros/ros.h>
#include <cmath>
#include <ctime>
#include <iostream>

// define gpio channels for each input required by the l298n 
#define In1		15
#define In2		14
#define EnA		18
#define In3		16
#define In4		20
#define EnB		19

int PWM_DC_Range;

double linear_range;
double angular_range;
double steering_maxDC;

 // +-----+-----+---------+------+---+---Pi 4B--+---+------+---------+-----+-----+
 // | BCM | wPi |   Name  | Mode | V | Physical | V | Mode | Name    | wPi | BCM |
 // +-----+-----+---------+------+---+----++----+---+------+---------+-----+-----+
 // |     |     |    3.3v |      |   |  1 || 2  |   |      | 5v      |     |     |
 // |   2 |   8 |   SDA.1 | ALT0 | 1 |  3 || 4  |   |      | 5v      |     |     |
 // |   3 |   9 |   SCL.1 | ALT0 | 1 |  5 || 6  |   |      | 0v      |     |     |
 // |   4 |   7 | GPIO. 7 |   IN | 1 |  7 || 8  | 1 | OUT  | TxD     | 15  | 14  |
 // |     |     |      0v |      |   |  9 || 10 | 1 | OUT  | RxD     | 16  | 15  |
 // |  17 |   0 | GPIO. 0 |   IN | 0 | 11 || 12 | 1 | ALT5 | GPIO. 1 | 1   | 18  |
 // |  27 |   2 | GPIO. 2 |   IN | 0 | 13 || 14 |   |      | 0v      |     |     |
 // |  22 |   3 | GPIO. 3 |   IN | 0 | 15 || 16 | 0 | IN   | GPIO. 4 | 4   | 23  |
 // |     |     |    3.3v |      |   | 17 || 18 | 0 | IN   | GPIO. 5 | 5   | 24  |
 // |  10 |  12 |    MOSI | ALT0 | 0 | 19 || 20 |   |      | 0v      |     |     |
 // |   9 |  13 |    MISO | ALT0 | 0 | 21 || 22 | 0 | IN   | GPIO. 6 | 6   | 25  |
 // |  11 |  14 |    SCLK | ALT0 | 0 | 23 || 24 | 1 | OUT  | CE0     | 10  | 8   |
 // |     |     |      0v |      |   | 25 || 26 | 1 | OUT  | CE1     | 11  | 7   |
 // |   0 |  30 |   SDA.0 |   IN | 1 | 27 || 28 | 1 | IN   | SCL.0   | 31  | 1   |
 // |   5 |  21 | GPIO.21 |   IN | 1 | 29 || 30 |   |      | 0v      |     |     |
 // |   6 |  22 | GPIO.22 |   IN | 1 | 31 || 32 | 0 | IN   | GPIO.26 | 26  | 12  |
 // |  13 |  23 | GPIO.23 |   IN | 1 | 33 || 34 |   |      | 0v      |     |     |
 // |  19 |  24 | GPIO.24 | ALT5 | 0 | 35 || 36 | 0 | OUT  | GPIO.27 | 27  | 16  |
 // |  26 |  25 | GPIO.25 |   IN | 0 | 37 || 38 | 0 | OUT  | GPIO.28 | 28  | 20  |
 // |     |     |      0v |      |   | 39 || 40 | 0 | IN   | GPIO.29 | 29  | 21  |
 // +-----+-----+---------+------+---+----++----+---+------+---------+-----+-----+
 // | BCM | wPi |   Name  | Mode | V | Physical | V | Mode | Name    | wPi | BCM |
 // +-----+-----+---------+------+---+---Pi 4B--+---+------+---------+-----+-----+

// function for gpio initialization
void _init()
{
	wiringPiSetupGpio();

	pinMode(In1, OUTPUT);
	pinMode(In2, OUTPUT);
	pinMode(EnA, PWM_OUTPUT);
	pinMode(In3, OUTPUT);
	pinMode(In4, OUTPUT);
	pinMode(EnB, PWM_OUTPUT);

	pwmSetMode(PWM_MODE_MS);	//mark space pwm mode, it is the classic way to intend a pwm signal, other option is balanced
	PWM_DC_Range = 1024;	// Duty Cycle range for PWMs signal 
	pwmSetRange (PWM_DC_Range);

	digitalWrite(In1, 0);
	digitalWrite(In2, 0);
    pwmWrite(EnA, 0);
	digitalWrite(In3, 0);
	digitalWrite(In4, 0);
	pwmWrite(EnB, 0);

	ROS_INFO_STREAM("GPIO initialization completed");
}

// function for extrapolation of the linear value from the cmd_vel message to duty cycle percentage
double cmd_vel_lin_conv(const geometry_msgs::Twist& msg)
{	
	return msg.linear.x/linear_range * PWM_DC_Range;		
}

// function for extrapolation of the angular value from the cmd_vel message to duty cycle percentage
double cmd_vel_ang_conv(const geometry_msgs::Twist& msg)
{
	return msg.angular.z/angular_range * (PWM_DC_Range * steering_maxDC);	//steering motion needs to be limited to 80%, due to the constuction condition
}

static void cmd_vel_act(const geometry_msgs::Twist& msg)
{  	
	double throttle = cmd_vel_lin_conv(msg);
	double steering = cmd_vel_ang_conv(msg);
	
	
	if(throttle <= (PWM_DC_Range*0.1)) 	// brake
	{
		digitalWrite(In1, 1);
		digitalWrite(In2, 1)
;		pwmWrite(EnA, 1024);
	}

	if (throttle > (PWM_DC_Range*0.1))		// backward
	{
		ROS_INFO_STREAM("Backward: " << throttle);
		digitalWrite(In1, 1);
		digitalWrite(In2, 0);
		pwmWrite(EnA, (int)throttle);
	}
	
	if (throttle < -(PWM_DC_Range*0.1))	// forward
	{
		throttle = abs(throttle);
		ROS_INFO_STREAM("Forward motion: " << throttle);
		digitalWrite(In1, 0);
		digitalWrite(In2, 1);
		pwmWrite(EnA, (int)throttle);
	}

	if (abs(steering) <= (PWM_DC_Range*0.05))	// steering to the center
	{
		digitalWrite(In3, 0);
		digitalWrite(In4, 0);
		digitalWrite(EnB, 1);
	}

	if (steering > (PWM_DC_Range*0.05))		// turn left
	{
		ROS_INFO_STREAM("Steering left: " << steering);
		digitalWrite(In3, 0);
		digitalWrite(In4, 1);
		pwmWrite(EnB, (int)steering);
	}

	if (steering < -(PWM_DC_Range*0.05))		// turn right
	{
		steering = abs(steering);
		ROS_INFO_STREAM("Steering right: "  << steering );
		digitalWrite(In3, 1);
		digitalWrite(In4, 0);
		pwmWrite(EnB, (int)steering);
	}
}

int main (int argc, char **argv)
{
	ros::init (argc, argv, "l298n_drive");

	ros::NodeHandle nh;

	nh.getParam("Legocar/linear_range", linear_range);
	nh.getParam("Legocar/angular_range", angular_range);
	nh.getParam("Legocar/steering_maxDC", steering_maxDC);

	_init();

	ros::Subscriber sub = nh.subscribe("/cmd_vel", 1, cmd_vel_act);

	ROS_INFO_STREAM("Lego Car READY!");

	ros::spin();

	return 0;
} 

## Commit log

2020-10-07 pwm modulation for velocity/stearing control
2020-10-15 readme update
    [Sketch.fzz]
2020-11-13 PID readme update
